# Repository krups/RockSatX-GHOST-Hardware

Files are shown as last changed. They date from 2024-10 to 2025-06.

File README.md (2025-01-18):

# RockSatX-GHOST-Hardware
PCB design files and documentation for the hardware used in the University of Kentucky's 2025 RockSat-XG KRUPS payload. Further information for each component is found in its respective folder.

### Hardware Folders
- [Capsule](Capsule)
- [FemtoSat](FemtoSat)
- [BaseStation/RocketStation](RocketStation)
- [LR62XE Adapter/Breakout](LR62XEAdapter)

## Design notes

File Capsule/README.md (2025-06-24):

# Capsule
PCB design files and documentation for the re-entry capsule used in the University of Kentucky's 2025 RockSat-XG KRUPS payload

### PCB Render
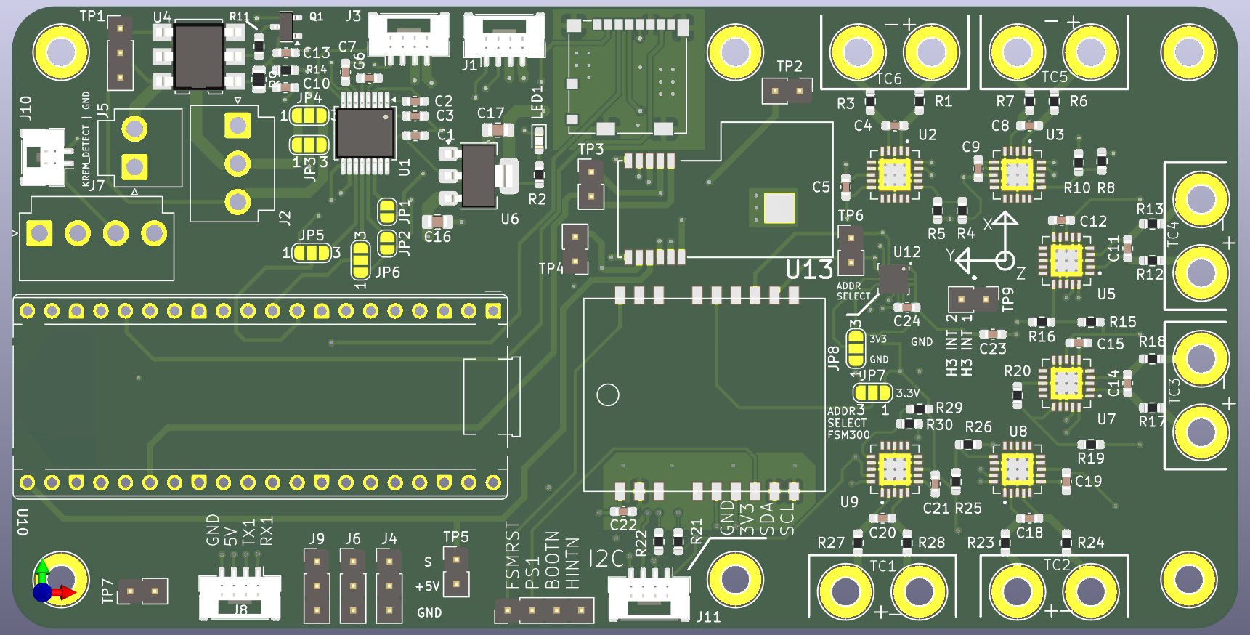
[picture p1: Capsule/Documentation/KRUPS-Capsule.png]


### Components
- [Raspberry Pi Pico 2 W (4MB Flash)](https://datasheets.raspberrypi.com/picow/pico-2-w-datasheet.pdf)
- [Fanstel LR62XE 1W 868/915MHz LoRa Modem](https://static1.squarespace.com/static/561459a2e4b0b39f5cefa12e/t/63ddc4b1dd728b424f1a6c23/1675478197953/LR62E_LR62XE_M262X840XE_Product+Specifications.pdf)
- [FSM300 9-Axis IMU](https://www.mouser.com/datasheet/2/1480/FSM30x_Datasheet-3196253.pdf)
- [H3LIS100DL 3-axis accelerometer](https://www.st.com/resource/en/datasheet/h3lis100dl.pdf)
- [MCP9600 thermocouple to digital converter](https://ww1.microchip.com/downloads/aemDocuments/documents/MSLD/ProductDocuments/DataSheets/MCP960X-L0X-RL0X-Thermocouple-EMF-to-Temperature-Converter-plus-minus-1-5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)

### Pin Mapping
| Pico 2 GPIO Pin | Net Name |
| --- | --- |
| GPIO0 | T_IRIDIUM |
| GPIO1 | R_IRIDIUM |
| GPIO2 | SDA |
| GPIO3 | SCL |
| GPIO4 | TX1 |
| GPIO5 | RX1 |
| GPIO6 | TX_GPS |
| GPIO7 | RX_GPS |
| GPIO12 | SD_SPI_MISO |
| GPIO13 | SD_SPI_CS |
| GPIO14 | SD_SPI_CLK |
| GPIO15 | SD_SPI_MOSI |
| GPIO16 | LORA_SPI_MISO |
| GPIO17 | LORA_SPI_CSN |
| GPIO18 | LORA_SPI_CLK |
| GPIO19 | LORA_SPI_MOSI |
| GPIO20 | LORA_ANTW |
| GPIO21 | LORA_RESET |
| GPIO22 | LORA_BUSY |
| GPIO26 | LORA_DIO1 |
| GPIO27 | PWMLS |

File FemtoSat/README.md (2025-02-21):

# KRUPS-FemtoSat
PCB design files and documentation for the femto-satellites used in the University of Kentucky's 2025 RockSat-XG KRUPS payload

### PCB Render
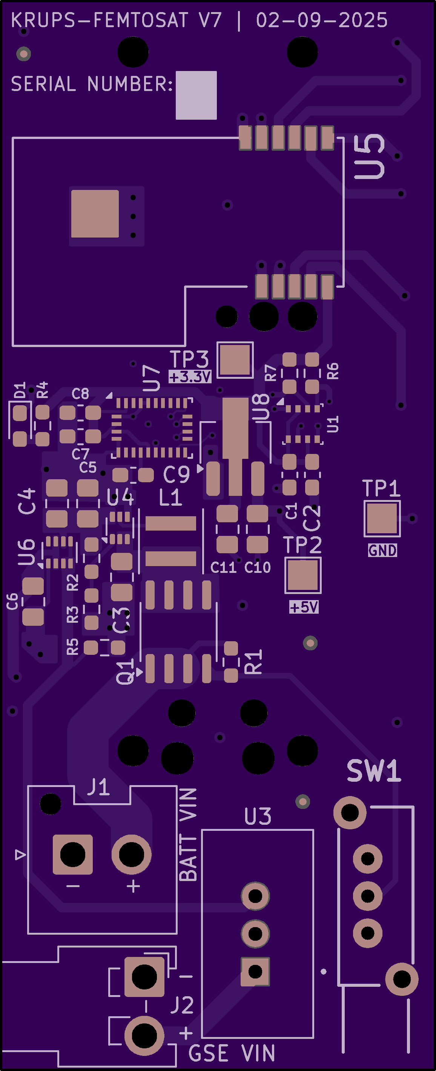
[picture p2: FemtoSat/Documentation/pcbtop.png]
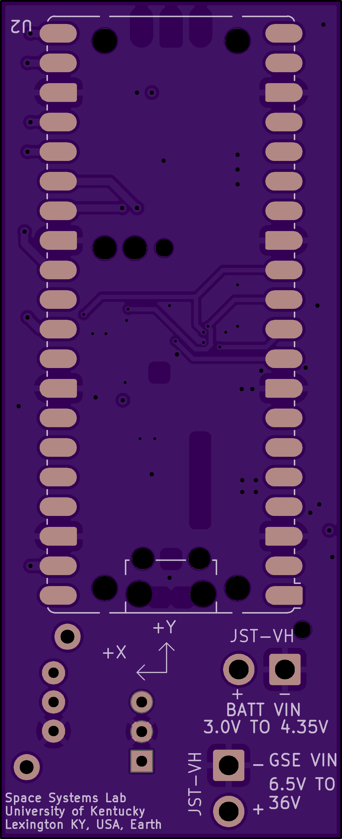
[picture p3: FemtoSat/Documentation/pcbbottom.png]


### Components
- [Raspberry Pi Pico 2 W (4MB Flash)](https://datasheets.raspberrypi.com/picow/pico-2-w-datasheet.pdf)
- [Fanstel LR62XE 1W 868/915MHz LoRa Modem](https://static1.squarespace.com/static/561459a2e4b0b39f5cefa12e/t/63ddc4b1dd728b424f1a6c23/1675478197953/LR62E_LR62XE_M262X840XE_Product+Specifications.pdf)
- [BME280 Temperature, Pressure, Humidity Sensor](https://www.bosch-sensortec.com/media/boschsensortec/downloads/datasheets/bst-bme280-ds002.pdf)
- [BNO086 9-Axis IMU](https://www.mouser.com/datasheet/2/1480/BNO080_085_Datasheet-3196201.pdf)

### Pin Mapping
| Pico 2 W GPIO Pin | Net Name |
| --- | --- |
| GPIO6 | BNO086_HINTN |
| GPIO7 | BNO086_RESET (active low)|
| GPIO8 | I2C_SDA |
| GPIO9 | I2C_SCL |
| GPIO16 | SPI_MISO |
| GPIO17 | SPI_NSS |
| GPIO18 | SPI_CLK |
| GPIO19 | SPI_MOSI |
| GPIO20 | LORA_ANTSW |
| GPIO21 | LORA_RESET (active low)|
| GPIO22 | LORA_BUSY |
| GPIO26 | LORA_DIO1 |

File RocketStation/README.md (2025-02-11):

# KRUPS-RocketStation
PCB design files and documentation for the base station/rocket station used in the University of Kentucky's 2025 RockSat-XG KRUPS payload

### PCB Render
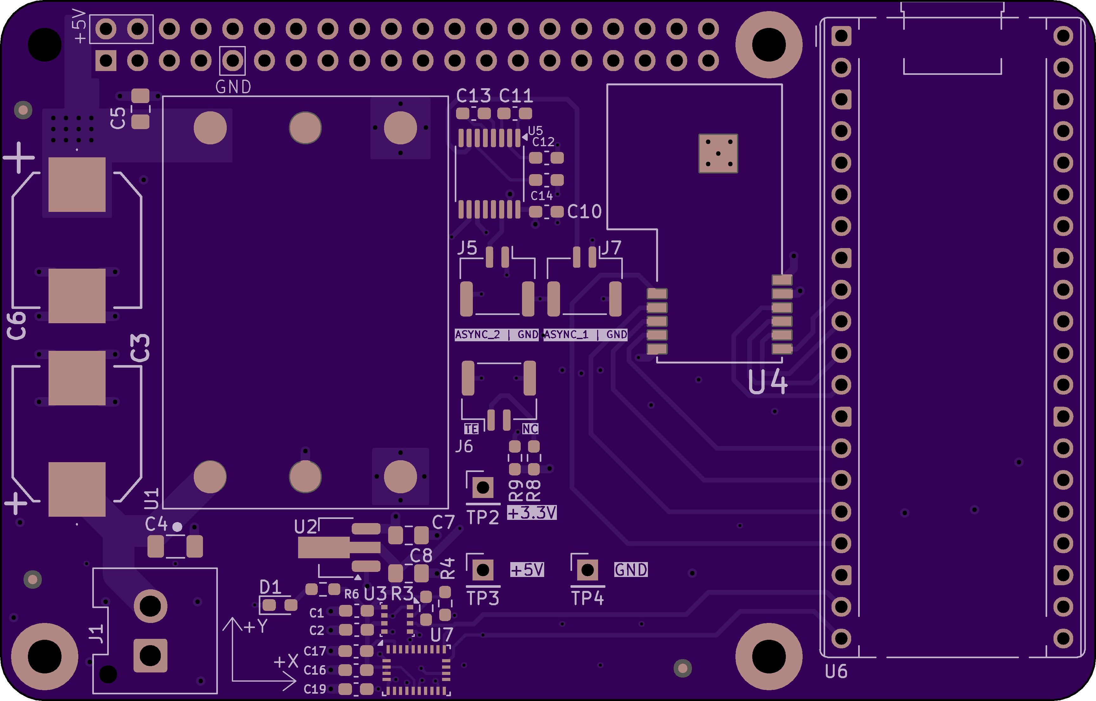
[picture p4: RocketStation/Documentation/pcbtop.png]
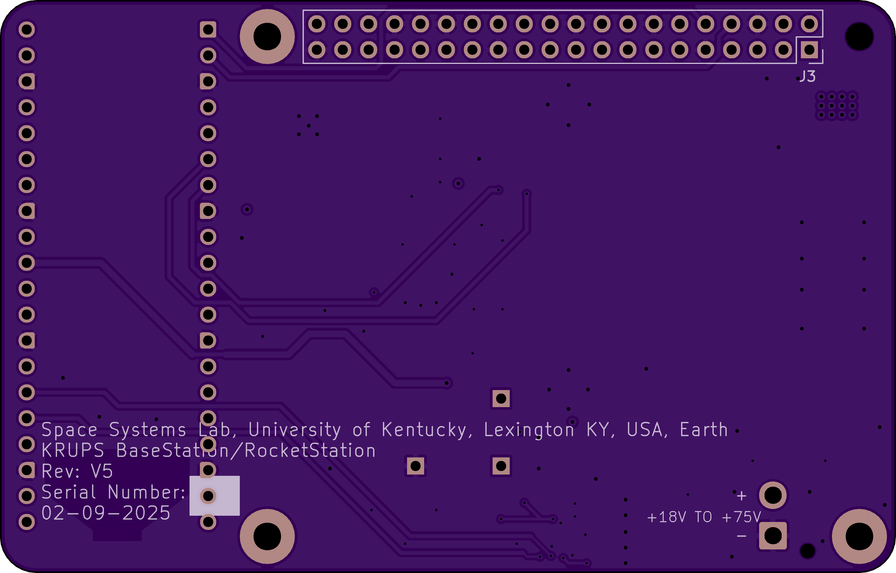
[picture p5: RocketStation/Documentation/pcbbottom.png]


### Components
- [Raspberry Pi Pico 2 W (4MB Flash)](https://datasheets.raspberrypi.com/picow/pico-2-w-datasheet.pdf)
- [Fanstel LR62XE 1W 868/915MHz LoRa Modem](https://static1.squarespace.com/static/561459a2e4b0b39f5cefa12e/t/63ddc4b1dd728b424f1a6c23/1675478197953/LR62E_LR62XE_M262X840XE_Product+Specifications.pdf)
- [BME280 Temperature, Pressure, Humidity Sensor](https://www.bosch-sensortec.com/media/boschsensortec/downloads/datasheets/bst-bme280-ds002.pdf)
- [BNO086 9-Axis IMU](https://www.mouser.com/datasheet/2/1480/BNO080_085_Datasheet-3196201.pdf)
- [PKU5511ESI DC/DC Step-down Converter](https://flexpowermodules.com/resources/fpm-techspec-pku5500e)

### Pin Mapping
| Pico 2 W GPIO Pin | Net Name |
| --- | --- |
| GPIO0 | RPI_UART4_TX |
| GPIO1 | RPI_UART4_RX |
| GPIO4 | ASYNC_UART_TX1 |
| GPIO5 | ASYNC_UART_TX2 |
| GPIO6 | SPI_CLK |
| GPIO7 | SPI_MOSI |
| GPIO8 | SPI_MISO |
| GPIO9 | SPI_NSS |
| GPIO10 | LORA_DIO1 |
| GPIO11 | LORA_BUSY |
| GPIO12 | LORA_RESET (active low)|
| GPIO13 | LORA_ANTSW |
| GPIO14 | I2C_SDA |
| GPIO15 | I2C_SCL |
| GPIO19 | BNO086_RESET (active low) |
| GPIO20 | BNO086_HINTN |
| GPIO26 | TE_SENSE (ADC) |

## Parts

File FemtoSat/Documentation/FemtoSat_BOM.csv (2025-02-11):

Reference | Value | Description | Qty | Digikey Part Number | DNP
C1,C2,C7,C8,C9 | 0.1u | 0.1uF, 16V, X7R, SMD 0603 | 5 | CC0603KRX7R7BB104
C3,C6,C10 | 10u | 10uF, 16V, X5R, SMD 0805 | 3 | CL21A106KOQNNNG
C4,C5,C11 | 22u | 22uF, 10V, X5R, SMD 0805 | 3 | CL21A226MPQNNNE
D1 | LED | LED, 1.95V Vf, 20mA If, SMD 0603 | 1 | APT1608SURCK
J1 | B2P-VH-FB-B | JST-VH 2 Pin Connector, Shielded, Vertical | 1 | B2P-VH-FB-B
J2 | B2PS-VH | JST-VH 2 Pin Connector, Horizontal | 1 | B2PS-VH
L1 | 1u | 1uH Inductor, Shielded | 1 | XEL4030-102MEC
Q1 | IRF7410 | PMOSFET, SOIC-8 | 1 | IRF7410TRPBF
R1,R5 | 100k | 100K OHM, 1%, 1/10W, SMD 0603 | 2 | RMCF0603FT100K
R2 | 73.2k | 73.2K OHM, 1%, 1/10W, SMD 0603 | 1 | RC0603FR-0773K2L
R3 | 10k | 10K OHM, 1%, 1/10W, SMD 0603 | 1 | RC0603FR-0710KL
R4 | 68 | 68 OHM, 5%, 1/10W, SMD 0603 | 1 | RC0603JR-0768RL
R6,R7 | 3.9k | 3.9K OHM, 1%, 1/10W, SMD 0603 | 2 | ERJ-3EKF3901V
SW1 | Enclosure Detector | SPDT Push Switch, Non-Latching | 1 | LC1258OANP
U1 | BME280 | 3-in-1 sensor, humidity, pressure, temperature, I2C and SPI interface, 1.71-3.6V, LGA-8 | 1 | BME280
U2 | Pico_2_W | Versatile and inexpensive microcontroller module powered by an RP2350 dual-core processor | 1 | 2648-SC1633CT-ND
U3 | TSR_2-2450 | 1A step-down regulator module, fixed 5V output voltage, 5-36V input voltage, -40°C to +85°C temperature range, TO-220 compatible LM78xx replacement | 1 | TSR 2-2450
U4 | TPS61023 | TPS61023 Boost Converter | 1 | TPS61023DRLR
U5 | LR62XE | 1W LoRa Module | 1 | LR62XE
U6 | TPS2117 | 2 Channnels Power Mux with Manual and Priority Switchover, 1.6-5.5V Input Voltage, 2.5A Output Current, Ron 40 mOhm, SOT-583-8 | 1 | TPS2117DRLR
U7 | BNO086 | Accelerometer, Gyroscope, Magnetometer, Temperature, 9 Axis Sensor IC, SPI Output | 1 | BNO086
U8 | AZ1117-3.3 | 1A 20V Fixed LDO Linear Regulator, 3.3V, SOT-89/SOT-223/TO-220/TO-252/TO-263 | 1 | AZ1117CR2-3.3TRG1

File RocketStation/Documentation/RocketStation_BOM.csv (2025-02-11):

Reference | Value | Description | Qty | DNP | Digikey Part Number
C1,C2,C10,C11,C12,C13,C14,C16,C17,C19 | 0.1u | 0.1uF, 16V, X7R, SMD 0603 | 10 |  | CC0603KRX7R7BB104
C3 | 100u | 100uF, 63V, Aluminum Electrolytic, SMD | 1 |  | A768MS107M1JLAV027
C4 | 2.2u | 2.2uF, 100V, X7R, SMD 1206 | 1 |  | 12061C225KAT2A
C5,C8 | 22u | 22uF, 10V, X5R, SMD 0805 | 2 |  | CL21A226MPQNNNE
C6 | 470u | 470uF, 25V, Aluminum Electrolytic, SMD | 1 |  | A768MS477M1ELAV017
C7 | 10u | 10uF, 16V, X5R, SMD 0805 | 1 |  | CL21A106KOQNNNG
D1 | LED | LED, 1.95V Vf, 20mA If, SMD 0603 | 1 |  | APT1608SURCK
J1 | B2P-VH-FB-B | JST-VH 2 Pin Connector, Shielded, Vertical | 1 |  | B2P-VH-FB-B
J3 | RPi5_Header | Expansion header for Raspberry Pi 5 | 1 |  | PRT-16764
J5,J6,J7 | BM02B-GHS-TBT | JST-GH 2 Pin Connector, Vertical | 3 |  | BM02B-GHS-TBT
R3,R4 | 3.9k | 3.9K OHM, 1%, 1/10W, SMD 0603 | 2 |  | ERJ-3EKF3901V
R6 | 68 | 68 OHM, 5%, 1/10W, SMD 0603 | 1 |  | RC0603JR-0768RL
R8 | 20k | 20K OHM, 1%, 1/10W, SMD 0603 | 1 |  | ERJ-3EKF2002V
R9 | 2k | 2K OHM, 1%, 1/10W, SMD 0603 | 1 |  | ERJ-3EKF2001V
U1 | PKU5511ESI | DC/DC Step Down, 1/16 brick | 1 |  | PKU5511ESI
U2 | AZ1117-3.3 | 1A 20V Fixed LDO Linear Regulator, 3.3V, SOT-89/SOT-223/TO-220/TO-252/TO-263 | 1 |  | AZ1117CR2-3.3TRG1
U3 | BME280 | 3-in-1 sensor, humidity, pressure, temperature, I2C and SPI interface, 1.71-3.6V, LGA-8 | 1 |  | BME280
U4 | LR62XE |  | 1
U5 | SP3232 | SP3232 RS-232 Level Shifter, TSSOP-16 | 1 |  | SP3232EUEY-L/TR
U6 | Pico_2_W | Versatile and inexpensive microcontroller module powered by an RP2350 dual-core processor | 1
U7 | BNO086 | Accelerometer, Gyroscope, Magnetometer, Temperature, 9 Axis Sensor IC, SPI Output | 1 |  | BNO086

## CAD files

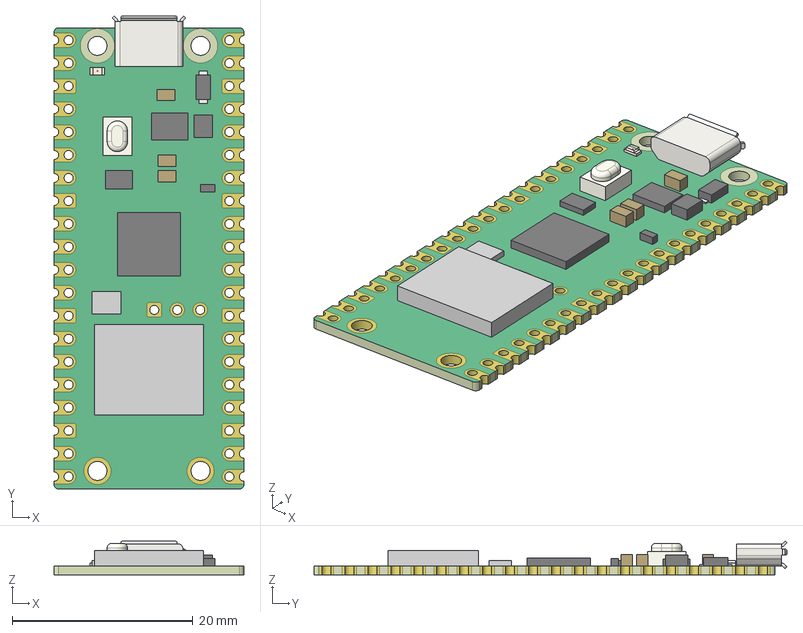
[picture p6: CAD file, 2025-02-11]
FemtoSat/KiCadProjectFiles/Imported/STEP/RaspberryPi_Pico_W.step
21.0 x 52.3 x 3.75 mm
Pico_W_Board
C1_47u
C2_47u
C21_47u
D1_MBR120VLSFT1G
D2_QSME-C194_Base
D2_QSME-C194_Phosphor
D2_QSME-C194_Lens
J1_690T505-x62-01x
L1_2u2
Q1_DMG1012T
SH1_CYW43439
SW1_TP-1221U-K9K5325
U1_RP2040
U2_RT6154AGQW
U3_W25Q16JVUXIQ
X1_X12M000000S096

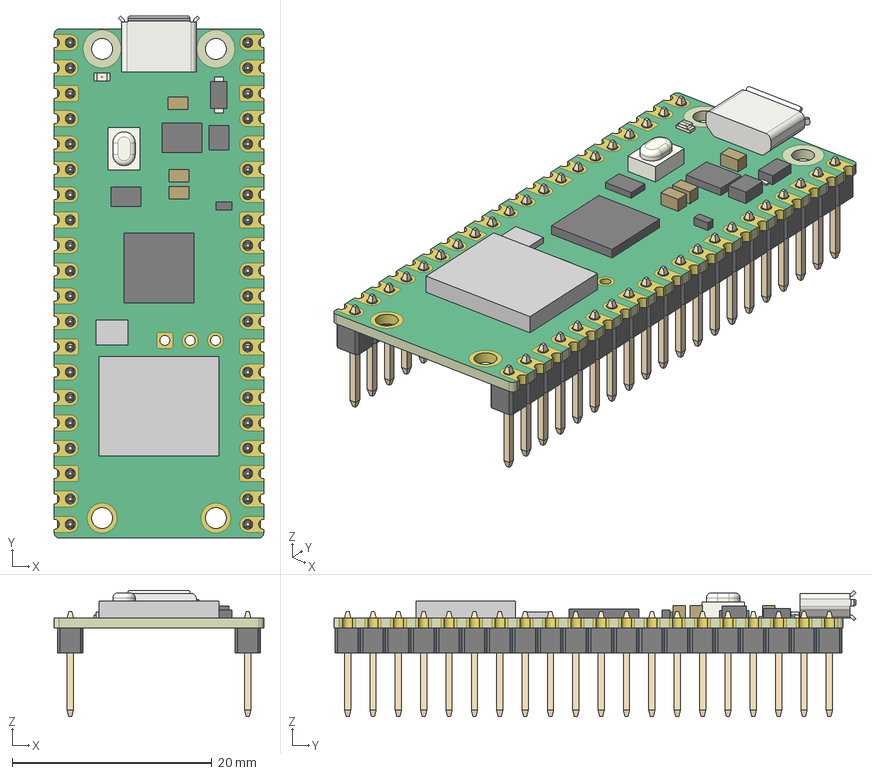
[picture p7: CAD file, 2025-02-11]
RocketStation/KiCadProjectFiles/Imported/STEP/RaspberryPi_Pico_W_AddedHeaders.step
21.0 x 52.3 x 12.6 mm
Pico_W_Board
C1_47u
C2_47u
C21_47u
D1_MBR120VLSFT1G
D2_QSME-C194_Base
D2_QSME-C194_Phosphor
D2_QSME-C194_Lens
J1_690T505-x62-01x
L1_2u2
Q1_DMG1012T
SH1_CYW43439
SW1_TP-1221U-K9K5325
U1_RP2040
U2_RT6154AGQW
U3_W25Q16JVUXIQ
X1_X12M000000S096
Header_Breakaway x 2

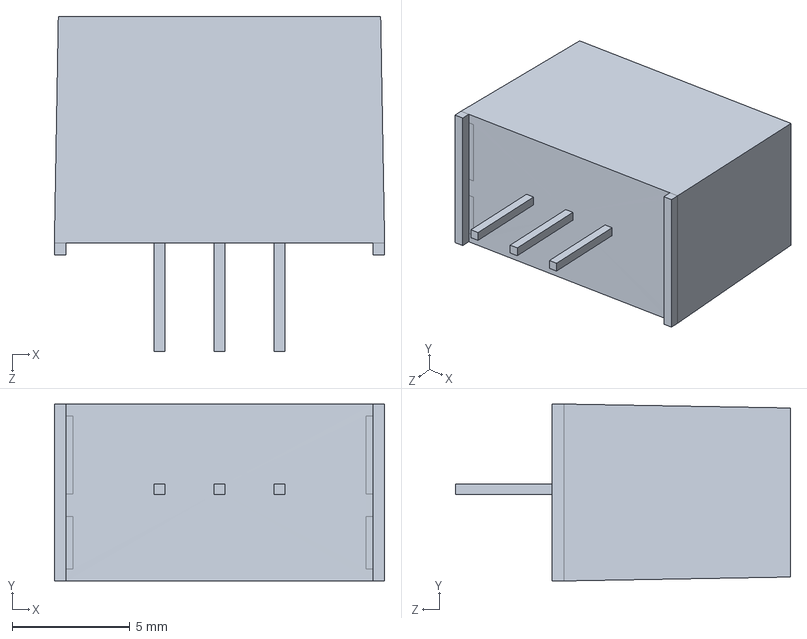
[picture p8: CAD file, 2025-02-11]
FemtoSat/KiCadProjectFiles/Imported/STEP/TSR2-2450.stp
14.0 x 7.50 x 14.2 mm

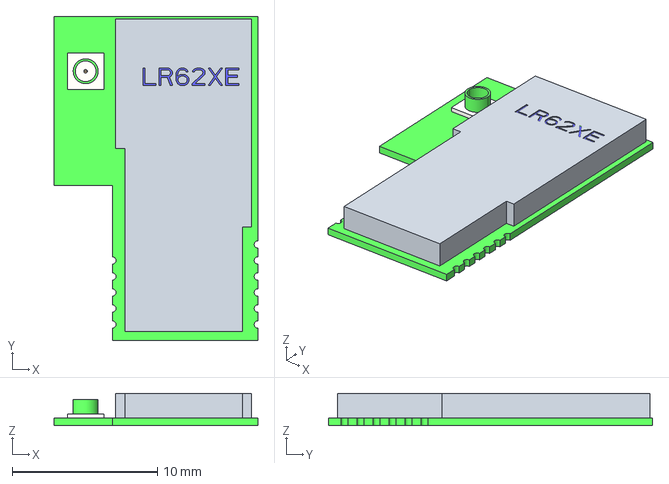
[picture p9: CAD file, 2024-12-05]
RocketStation/KiCadProjectFiles/Imported/STEP/lr62xe.stp
14.0 x 22.3 x 2.20 mm

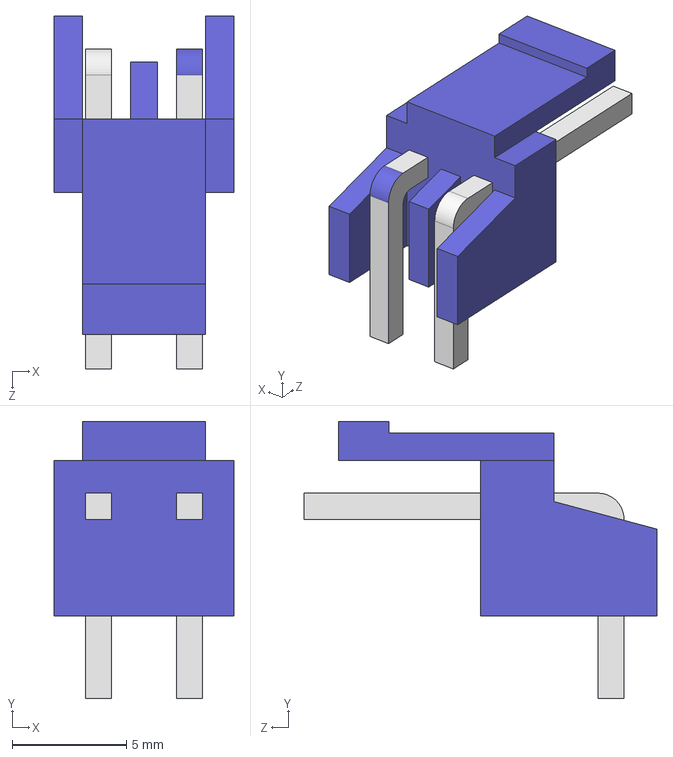
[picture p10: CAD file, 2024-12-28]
FemtoSat/KiCadProjectFiles/Imported/STEP/S2P-VH.STEP
7.86 x 12.1 x 15.4 mm

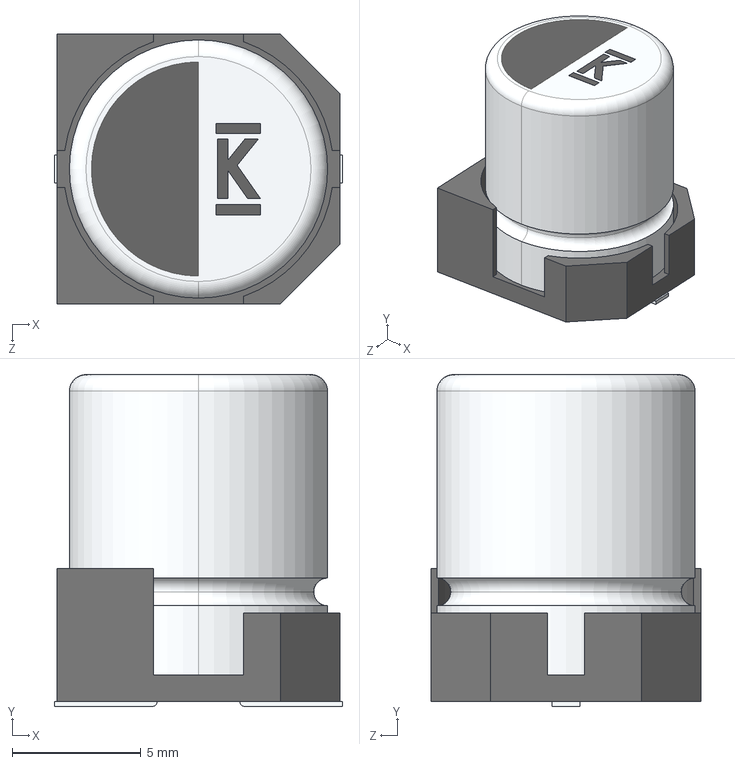
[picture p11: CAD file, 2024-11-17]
RocketStation/KiCadProjectFiles/Imported/STEP/A768MS.step
11.2 x 12.9 x 10.5 mm

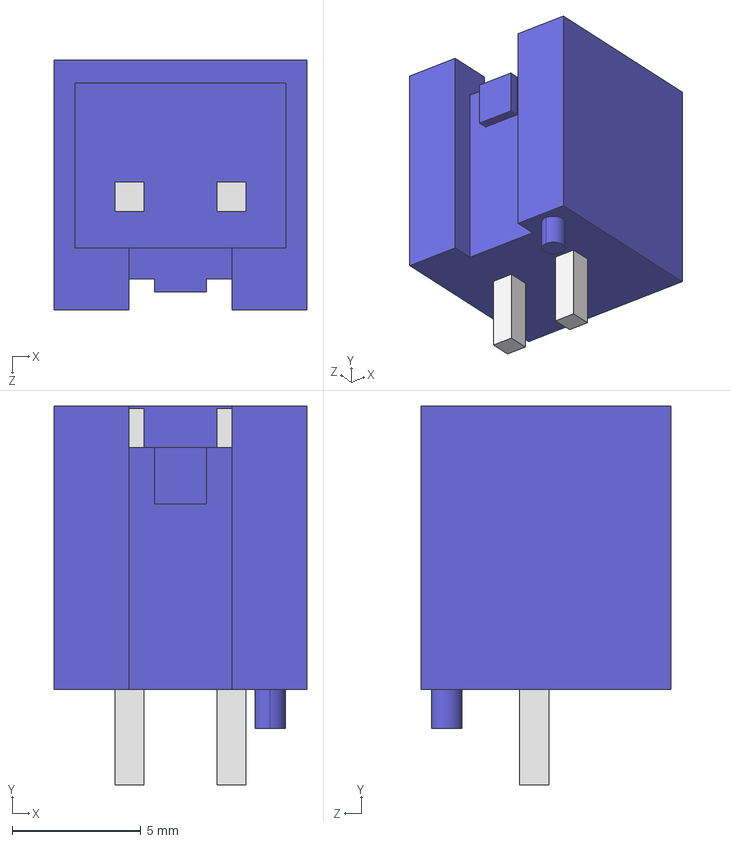
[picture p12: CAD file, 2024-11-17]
FemtoSat/KiCadProjectFiles/Imported/STEP/B2P-VH-FB-B.STEP
9.80 x 14.7 x 9.70 mm

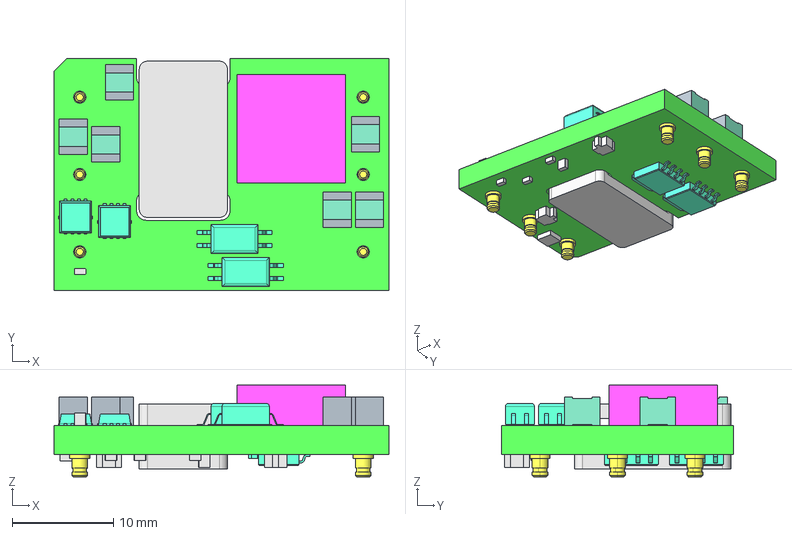
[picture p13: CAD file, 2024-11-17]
RocketStation/KiCadProjectFiles/Imported/STEP/PKU5511ESI.stp
33.0 x 22.9 x 9.04 mm
SNF901066 x 6
C2 x 6
M1 x 2
OP2 x 2
Ferrite-core x 2
chock
C26 x 3
T210 x 2
R15 x 2
Mosfet1 x 2
X.RYN1214604.2F.2
BOARD_PART

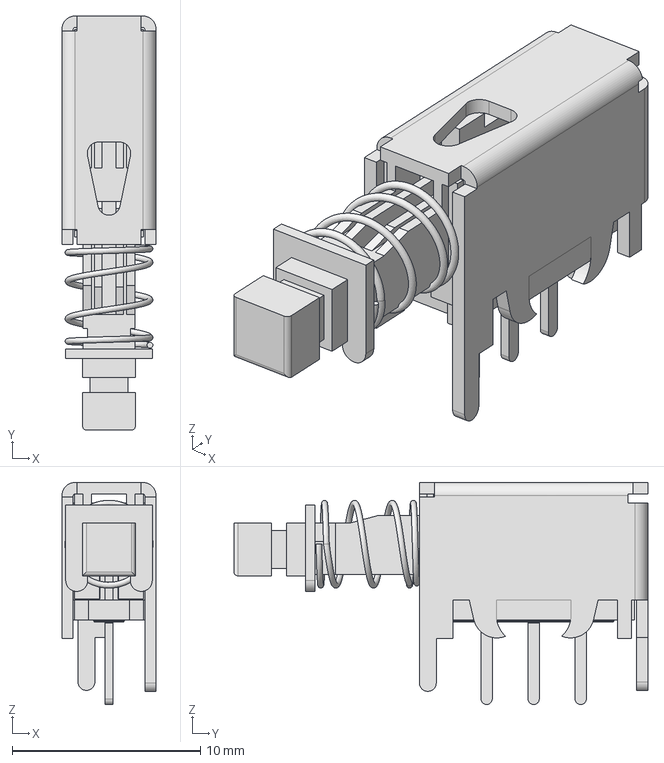
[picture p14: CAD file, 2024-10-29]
FemtoSat/KiCadProjectFiles/Imported/STEP/LC1258OANP.stp
5.00 x 22.0 x 11.8 mm

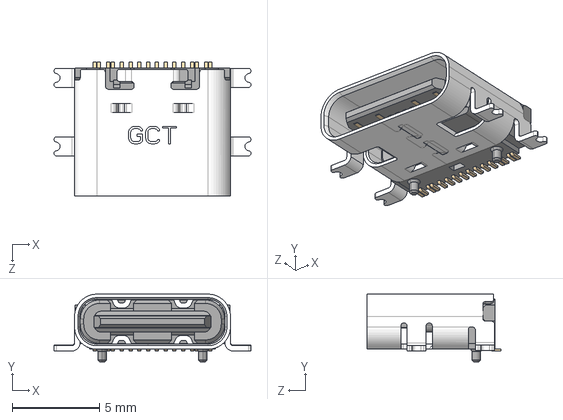
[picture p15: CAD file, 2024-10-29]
RocketStation/KiCadProjectFiles/Imported/STEP/USB4110GFA.step
11.3 x 3.89 x 7.70 mm

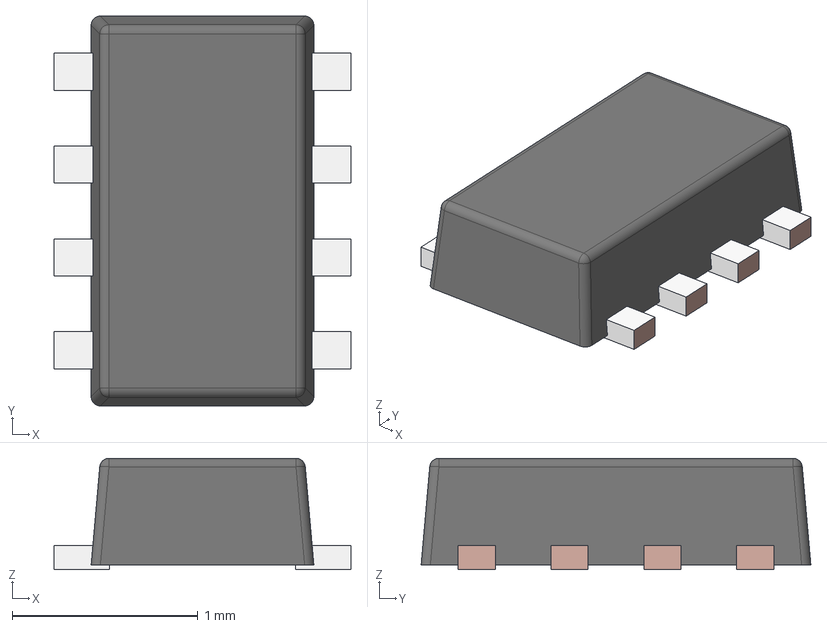
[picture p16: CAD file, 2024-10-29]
FemtoSat/KiCadProjectFiles/Imported/STEP/SOT-583.stp
1.60 x 2.10 x 0.6 mm
FRAME-DRL0008A
BODY-SOT

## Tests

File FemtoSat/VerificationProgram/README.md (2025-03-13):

## Femtosat Verification Program

Simple program that uses a pico debugger to verify that the BME280, BNO086, and LR62XE on a newly assembled femtosat are working. 

## Usage
Import this folder as a project into the VS Code Raspberry Pi Pico extension:
1. Set up your Raspberry Pi Pico development environment by following chapter 3 of [this](https://datasheets.raspberrypi.com/pico/getting-started-with-pico.pdf) guide
2. Clone this repo and its submodules using your preferred method.
- If you're new to git, I'd recommend [Github Desktop](https://github.com/apps/desktop).
- If you're downloading a zip archive from Github, make sure that you download each linked submodule (external repositories linked in the lib folder) manually as they will not be included.
2. Click "Import Project" under the General tab from within the extension.
3. Select the location of this folder
4. Change the debugger from DebugProbe to SWD (If you're using a pico to debug. If you're using the debug probe, leave it as-is.)
5. Click "Import"
6. Click "Configure CMake" under the Project tab from within the extension.
7. Set a debugging breakpoint in main.cpp in the src folder. It should be near line 121, with a comment saying BREAKPOINT HERE
8. Power on the femtosat with a bench top power supply. 9V to the GSE input usually works fine. Pay attention to polarity.
9. Connect the debugger wires to the debugging header on the pico. 
- Starting from the board edge going to the center, the wire colors should be orange, black, yellow (with the pico debug probe).
10. Debug the project from the pico extension window. This will start a debugging session.
11. Continue the debugging session until you hit the breakpoint set earlier
12. Verify that the initialization state variables in the debugger match the expected values. 
- If not, that sensor is not operational. Check solder joints and replace the component if necessary.
- Error code specifics can be found [here](https://jgromes.github.io/RadioLib/group__status__codes.html) for the LoRa module, and within lib\BME280_Drivers\bme280_defs.h for the BME280. The BNO086 does not give any useful error codes.

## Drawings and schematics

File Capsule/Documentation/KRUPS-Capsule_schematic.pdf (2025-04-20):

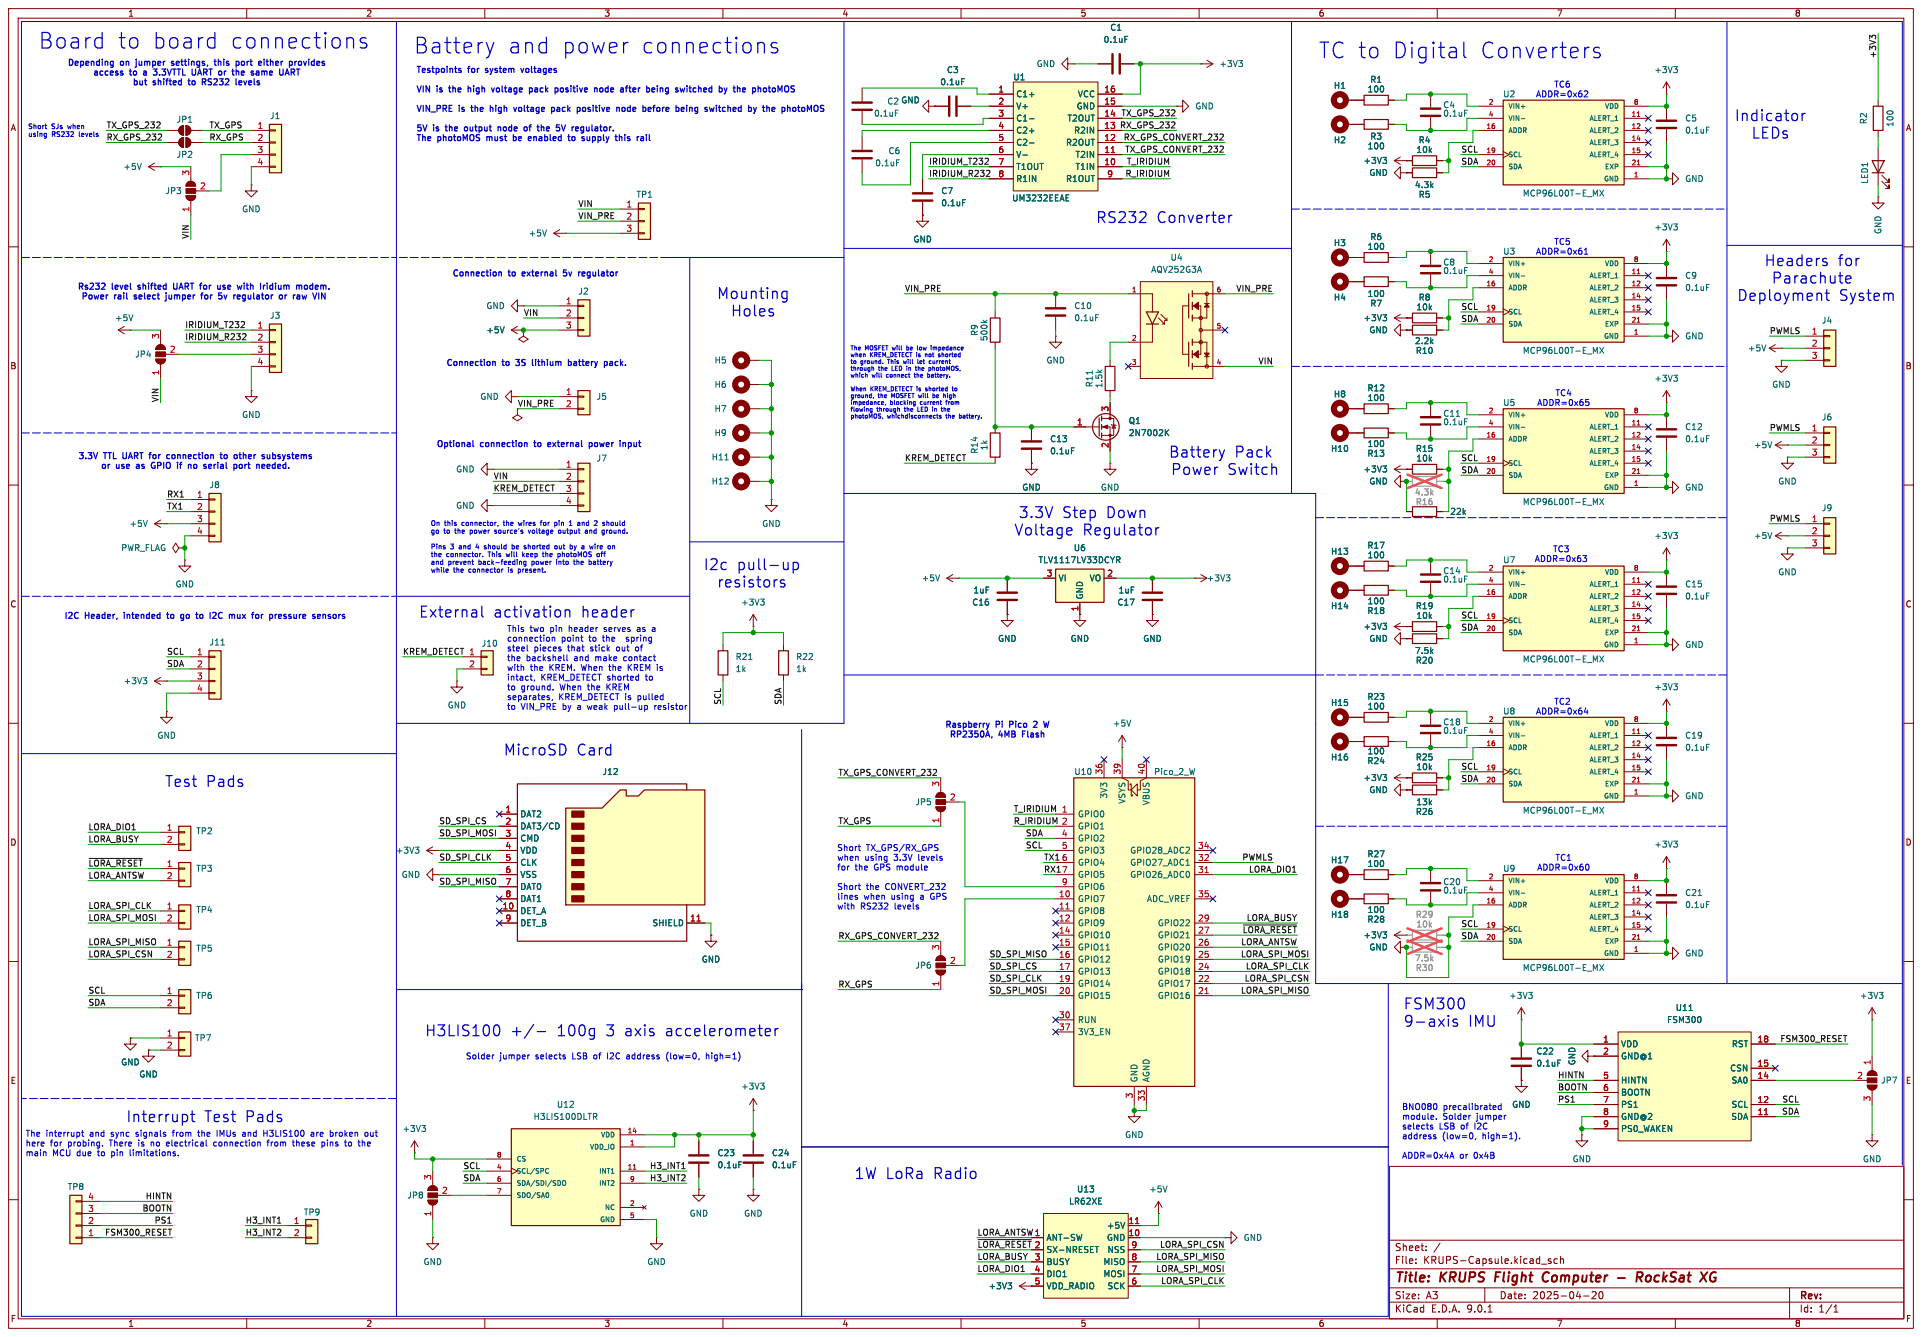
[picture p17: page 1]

T_IRIDIUM Board to board connections

TC to Digital Converters

Depending on jumper settings, this port either provides
access to a 3.3VTTL UART or the same UART

VIN_PRE is the high voltage pack positive node before being switched by the photoMOS

Connection to external 5v regulator
H6 GND

3.3V TTL UART for connection to other subsystems or use as GPIO if no serial port needed. Rs232 level shifted UART for use with Iridium modem. Power rail select jumper for 5v regulator or raw VIN

The MOSFET will be low impedance when KREM_DETECT is not shorted

Connection to 3S lithium battery pack.

Optional connection to external power input
0.1uF GND GND

steel pieces that stick out of

to ground. When the KREM

RP2350A, 4MB Flash Short TX_GPS/RX_GPS when using 3.3V levels

TC1 ADDR=0x60 BNO080 precalibrated module. Solder jumper selects LSB of I2C

for the GPS module Short the CONVERT_232

lines when using a GPS with RS232 levels

Id: 1/1 Title: KRUPS Flight Computer - RockSat XG

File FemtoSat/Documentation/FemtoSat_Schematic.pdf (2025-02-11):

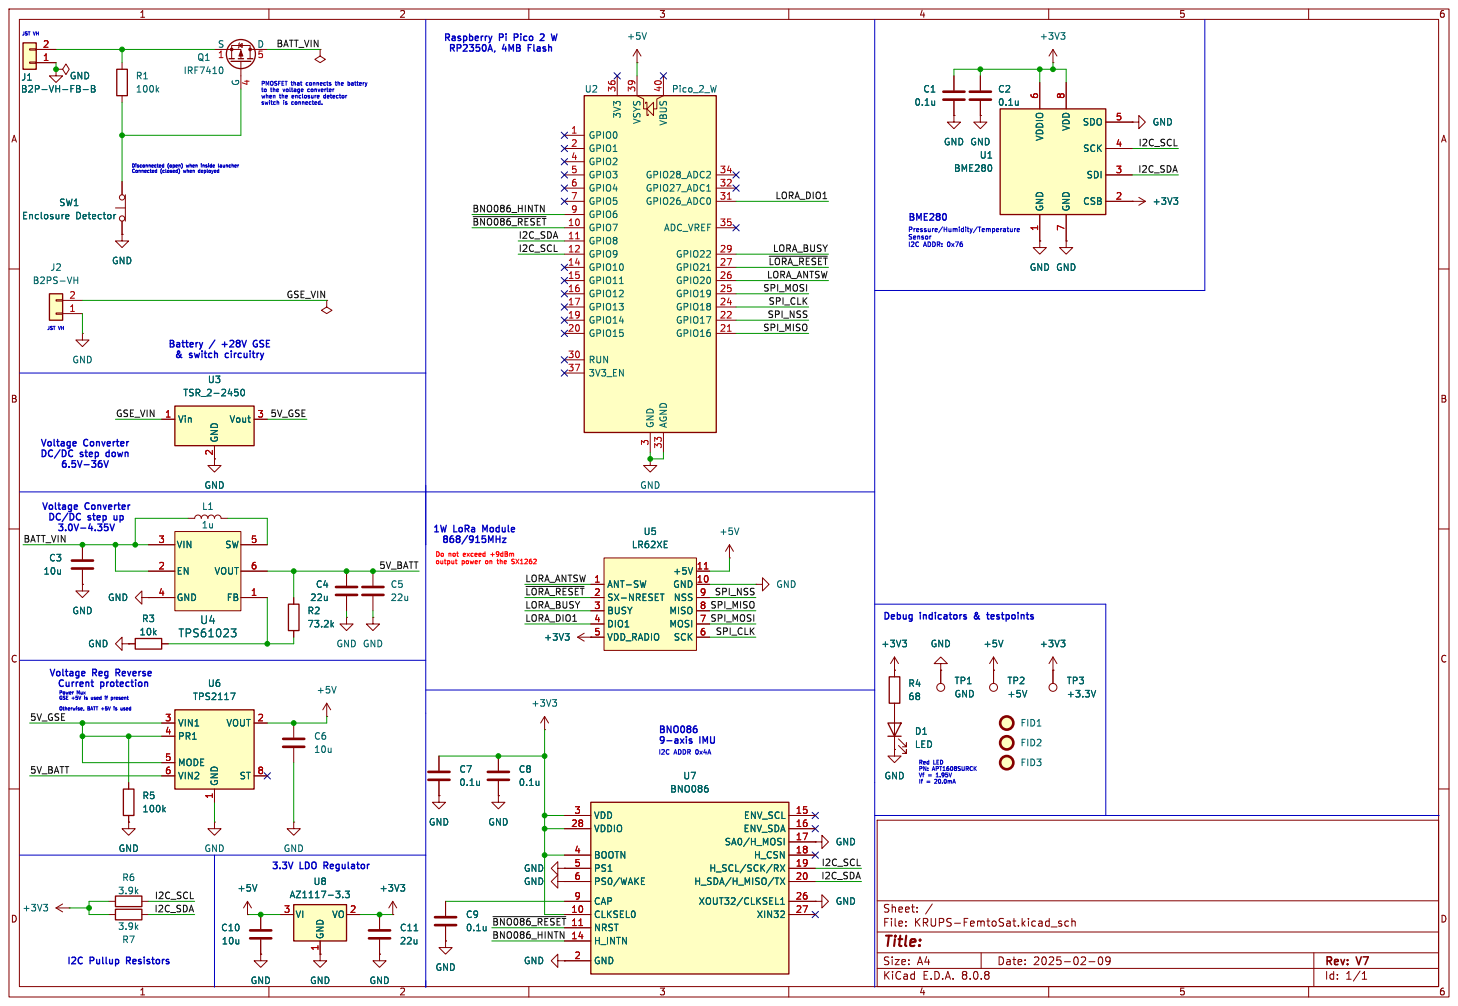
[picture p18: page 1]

1 CSB 2 SDI 3 SCK 4 SDO 5 VDDIO

BME280 Voltage Converter DC/DC step up

868/915MHz Voltage Converter DC/DC step down

1 VOUT 2 VIN1 3 PR1 4 MODE 5 VIN2 6 ST 8 GND GND

1 VOUT 2 VIN1 3 PR1 4 MODE 5 VIN2 6 ST 8 U6 TPS2117 GND

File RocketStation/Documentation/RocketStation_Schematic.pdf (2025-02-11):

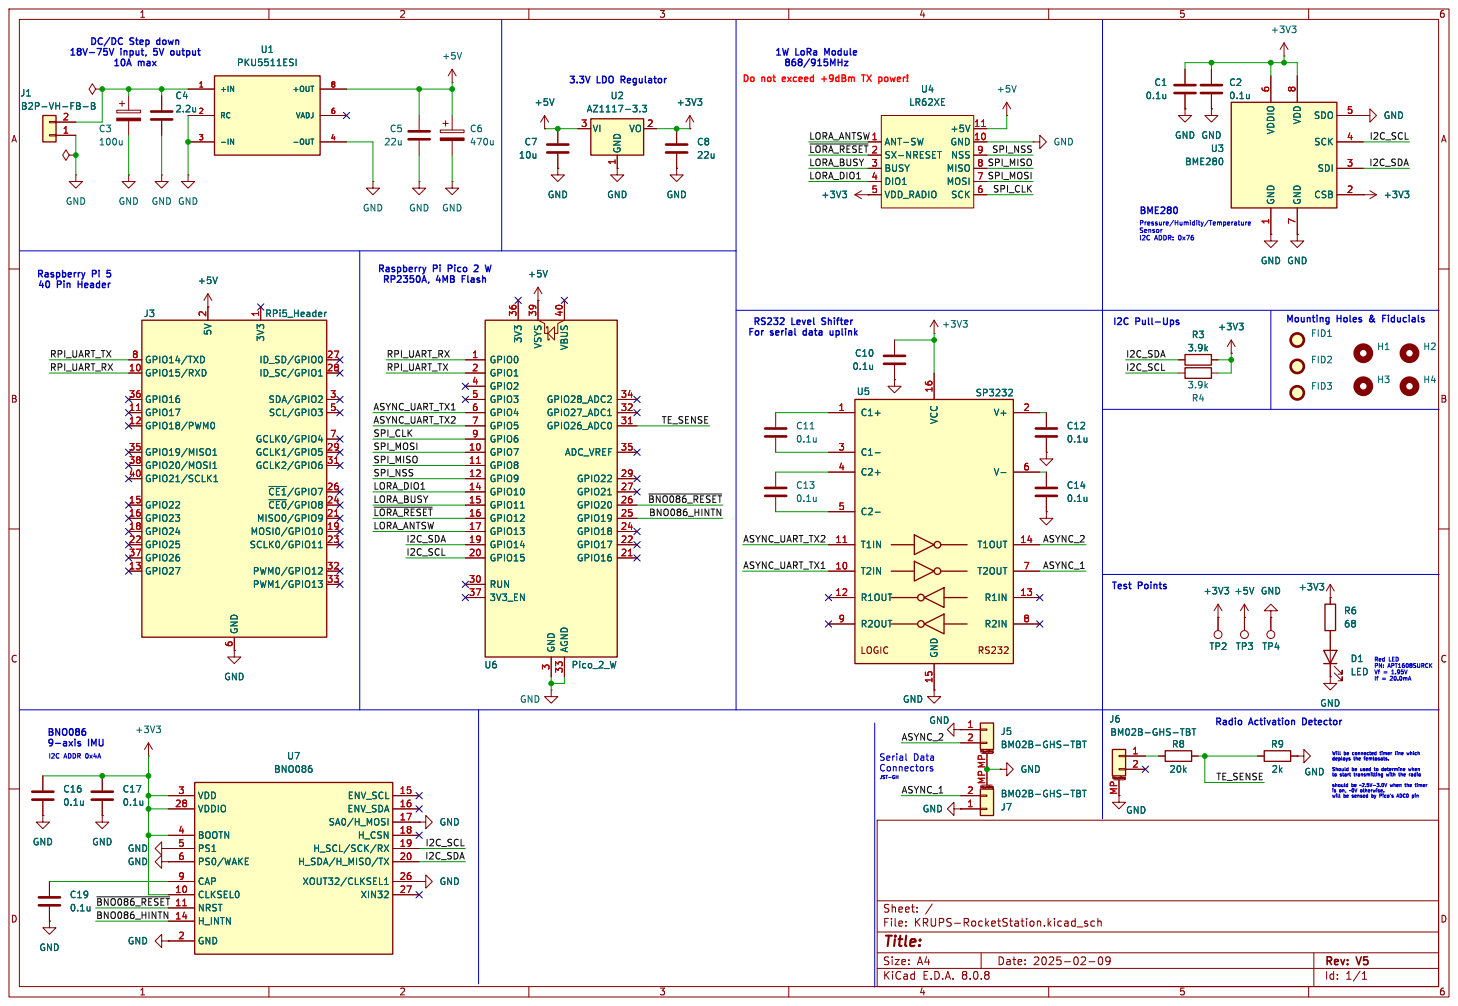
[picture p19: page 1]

DC/DC Step down

1 CSB 2 SDI 3 SCK 4 SDO 5 VDDIO

Pressure/Humidity/Temperature Sensor

If = 20.0mA Raspberry Pi Pico 2 W
RP2350A, 4MB Flash

6 GCLK0/GPIO4 7 GPIO14/TXD 8 +5V U7 BNO086 CLKSEL0 10 NRST 11 H_INTN 14 ENV_SCL 15 ENV_SDA 16 SA0/H_MOSI 17 H_CSN 18 H_SCL/SCK/RX 19 GND 2 H_SDA/H_MISO/TX 20 XOUT32/CLKSEL1 26 XIN32 27 VDDIO 28 VDD 3 BOOTN 4 PS1 5 PS0/WAKE 6 CAP 9 GND GND

J5BM02B-GHS-TBT GND GND

Id: 1/1 Title: File: KRUPS-RocketStation.kicad_sch Sheet: / GND

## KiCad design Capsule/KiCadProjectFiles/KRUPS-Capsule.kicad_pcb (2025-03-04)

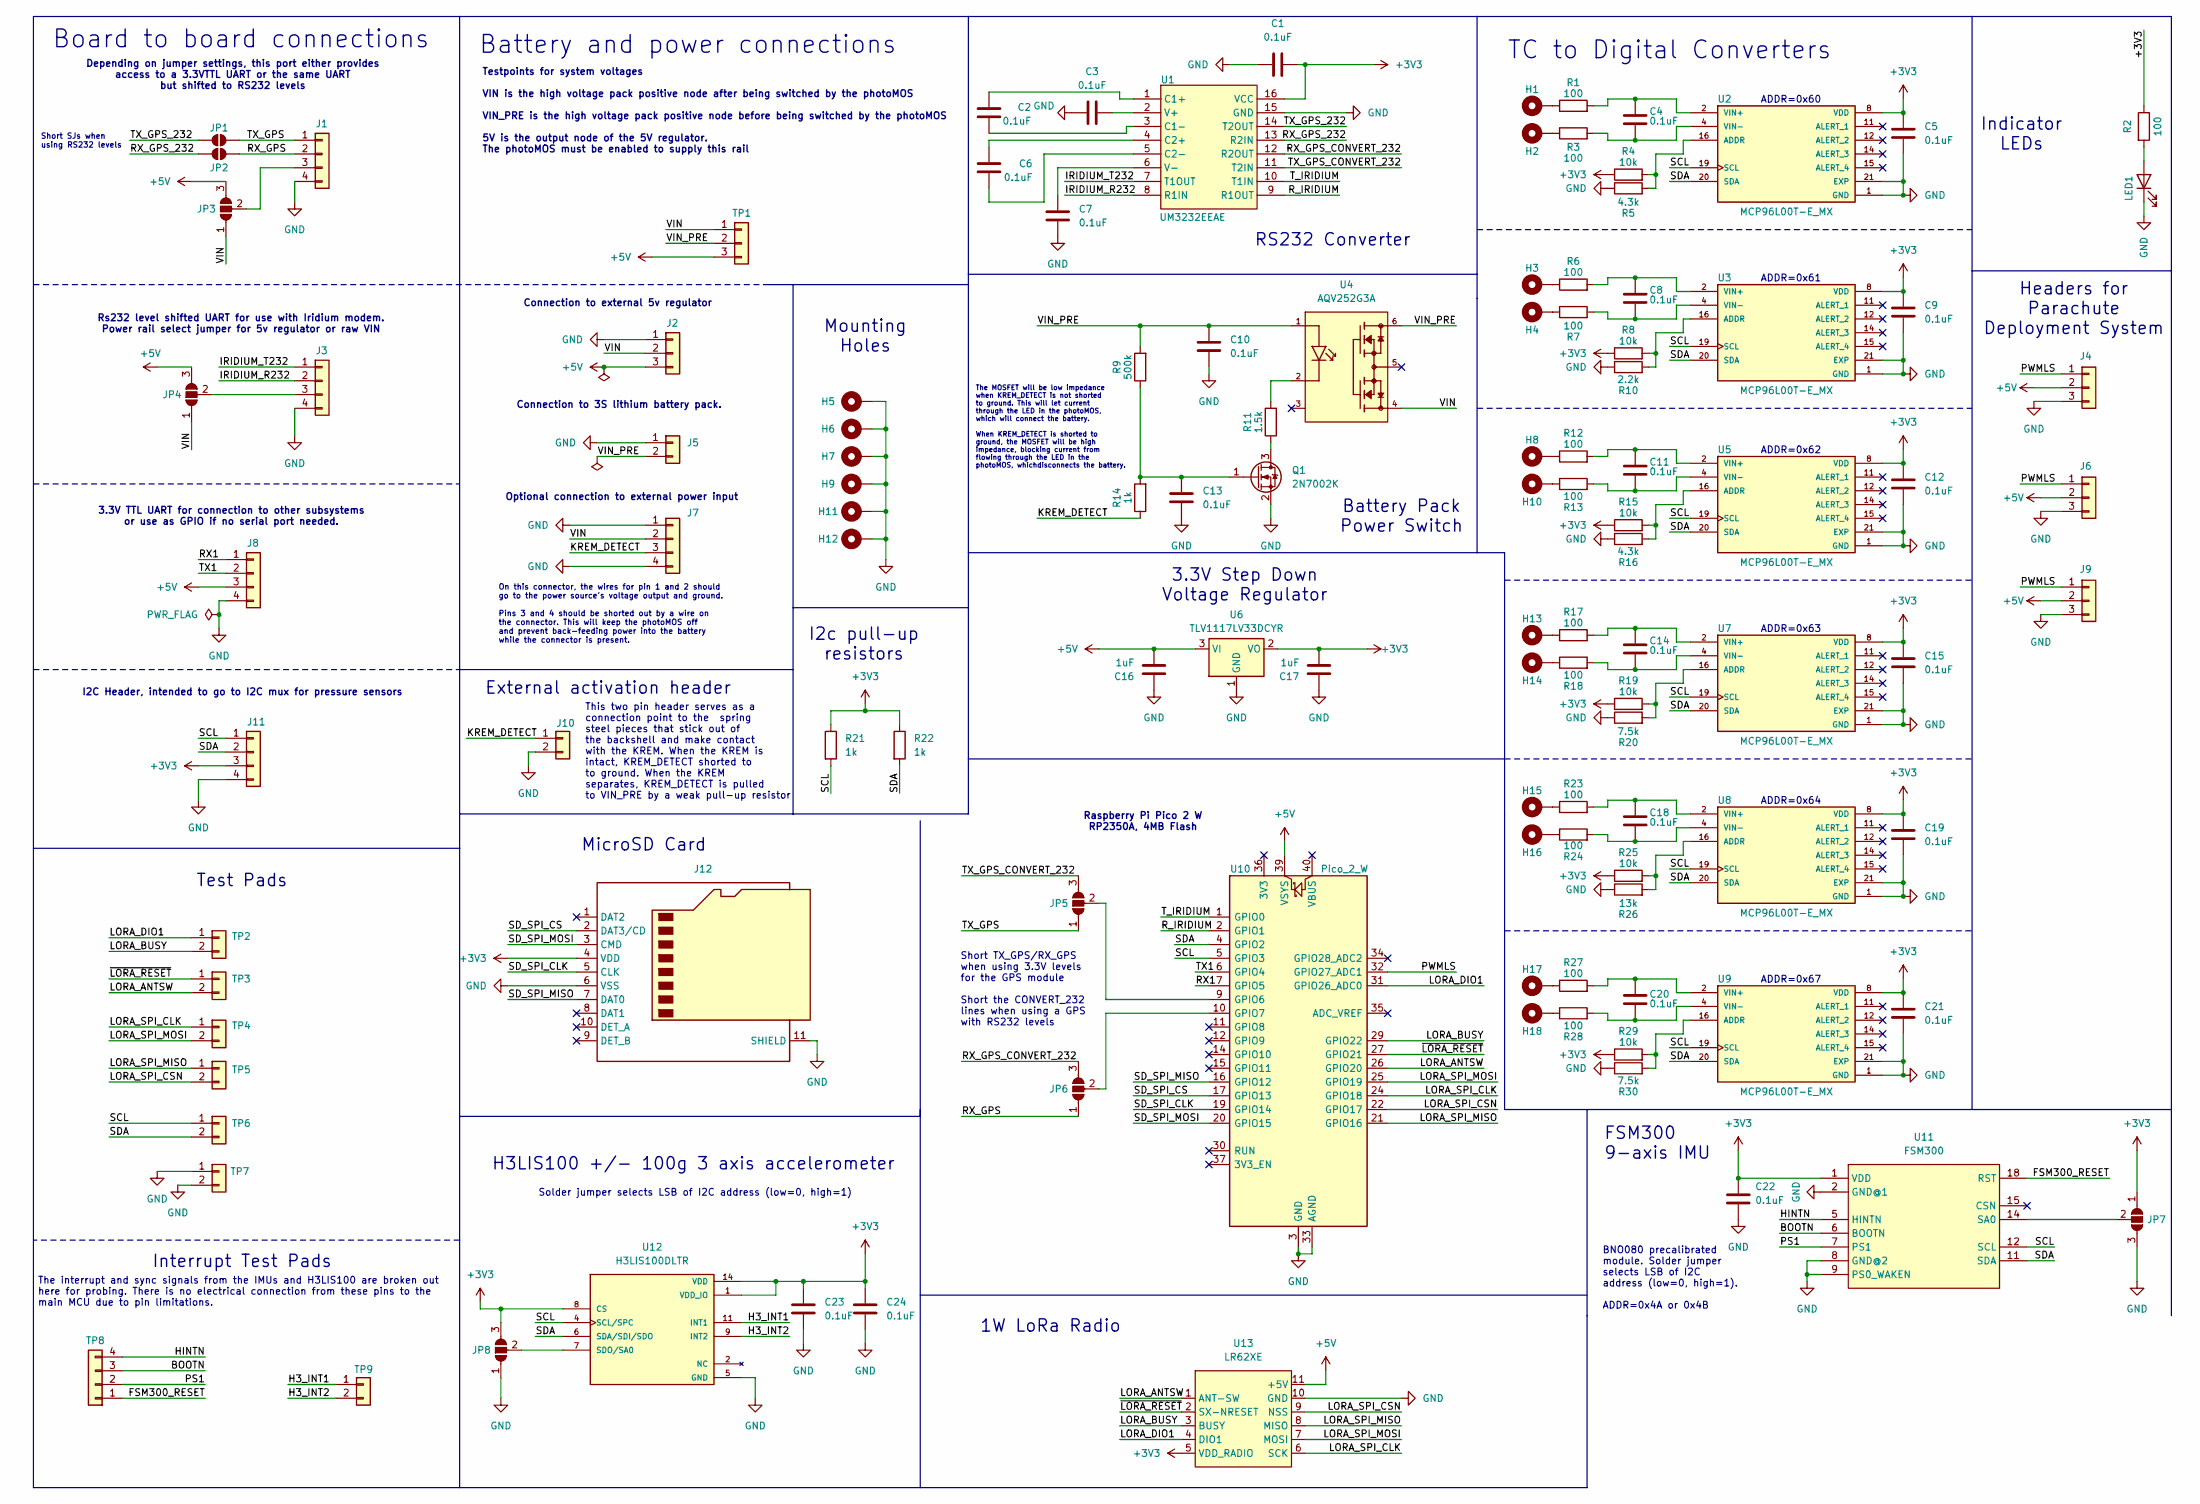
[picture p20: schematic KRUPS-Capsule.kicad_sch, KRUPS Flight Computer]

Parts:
C1, C2, C3, C4, C5, C6, C7, C8, C9, C10, C11, C12, C13, C14, C15, C18, C19, C20, C21, C22, C23, C24: 0.1uF; C_0603_1608Metric_Pad1.08x0.95mm_HandSolder; Digikey Part Number 0603B104K500XD
C16, C17: 1uF; C_0805_2012Metric_Pad1.18x1.45mm_HandSolder; Digikey Part Number 3372-0805B105K100CCTR-ND
H1, H2, H3, H4, H5, H6, H7, H8, H9, H10, H11, H12, H13, H14, H15, H16, H17, H18: MountingHole_Pad; 2,8-PAD
J1, J3: JST_GH_BM04B; JST_GH_BM04B-GHS-TBT_1x04-1MP_P1.25mm_Vertical; Digikey Part Number 455-BM04B-GHS-TBTTR-ND
J2: JST_VH_B4P-VH-B; JST_VH_B3P-VH-B_1x03_P3.96mm_Vertical; Digikey Part Number 455-B4P-VH-B-ND
J4, J6, J9: PinHeader_1x03_P2.54mm_Vertical; Digikey Part Number 732-5316-ND
J5: JST_VH_B2P; JST_VH_B2P-VH-B_1x02_P3.96mm_Vertical; Digikey Part Number 455-1639-ND
J7: Conn_01x04; JST_VH_B4P-VH-B_1x04_P3.96mm_Vertical; Digikey Part Number 455-B4P-VH-ND
J8: JST_GH_BM04B-GHS; JST_GH_BM04B-GHS-TBT_1x04-1MP_P1.25mm_Vertical; Digikey Part Number 455-1566-2-ND
J10: JST_GH_BM02B-GHS-TBT_1x02-1MP_P1.25mm_Vertical; Digikey Part Number 455-1564-2-ND
J11: BM04B-JST-GH; JST_GH_BM04B-GHS-TBT_1x04-1MP_P1.25mm_Vertical; Digikey Part Number 455-1566-2-ND
J12: Micro_SD_Card_Det2; microSD_HC_Molex_104031-0811; Digikey Part Number WM6357TR-ND
JP1, JP2: SolderJumper_2_Open; SolderJumper-2_P1.3mm_Open_RoundedPad1.0x1.5mm
JP3, JP4, JP5, JP6, JP7, JP8: SolderJumper_3_Open; SolderJumper-3_P1.3mm_Open_RoundedPad1.0x1.5mm_NumberLabels
LED1: LED; LED_0603_1608Metric_Pad1.05x0.95mm_HandSolder; Digikey Part Number 2679-CTL0603FYW1TTR-ND
Q1: 2N7002K; SOT-23; Digikey Part Number 2N7002KTR-ND
R1, R2, R3, R6, R7, R12, R13, R17, R18, R23, R24, R27, R28: 100; R_0603_1608Metric_Pad0.98x0.95mm_HandSolder; Digikey Part Number 311-100GRTR-ND
R4, R8, R15, R19, R25, R29: 10k; R_0603_1608Metric_Pad0.98x0.95mm_HandSolder; Digikey Part Number 13-RC0603FR-1310KLTR-ND
R5, R16: 4.3k; R_0603_1608Metric_Pad0.98x0.95mm_HandSolder; Digikey Part Number P4.30KHTR-ND
R9: 500k; R_0805_2012Metric; Digikey Part Number 738-RNCF0805BTE500KTR-ND
R10: 2.2k; R_0603_1608Metric_Pad0.98x0.95mm_HandSolder; Digikey Part Number 311-2.2KGRTR-ND
R11: 1.5k; R_0603_1608Metric_Pad0.98x0.95mm_HandSolder; Digikey Part Number 408-1766-2-ND
R14, R21, R22: 1k; R_0603_1608Metric_Pad0.98x0.95mm_HandSolder; Digikey Part Number 311-1.0KGRTR-ND
R20, R30: 7.5k; R_0603_1608Metric_Pad0.98x0.95mm_HandSolder; Digikey Part Number 311-7.5KDTR-ND
R26: 13k; R_0603_1608Metric_Pad0.98x0.95mm_HandSolder; Digikey Part Number 541-13.0KHTR-ND
TP1: Conn_01x03; PinHeader_1x03_P2.54mm_Vertical; Digikey Part Number 732-5316-ND
TP2, TP3, TP4, TP5, TP6, TP7: TEST POINT; PinHeader_1x02_P2.54mm_Vertical; Digikey Part Number 732-5315-ND
TP8: PinHeader_1x04_P2.54mm_Vertical; Digikey Part Number 732-5317-ND
TP9: Conn_01x02; PinHeader_1x02_P2.54mm_Vertical; Digikey Part Number 732-5315-ND
U1: UM3232EEAE; SSOP-16_5.3x6.2mm_P0.65mm; Digikey Part Number UM3232EEAE
U2, U3, U5, U7, U8, U9: MCP96L00T-E_MX; QFN65P500X500X100-21N_MCP96L00T-E_MX; Digikey Part Number MCP96L00T-E/MXTR-ND
U4: AQV252G3A; SMDIP-6_W7.62mm; Digikey Part Number 255-6561-ND
U6: TLV1117LV33DCYR; SOT-223-3_TabPin2; Digikey Part Number 296-28778-2-ND
U10: Pico_2_W; RaspberryPi_Pico_Common_THT; Digikey Part Number 2648-SC1633CT-ND
U11: FSM300; FSM300_FOOTPRINT; Digikey Part Number 1888-1001-ND
U12: H3LIS100DLTR; LGA-16_3x3mm_P0.5mm_LayoutBorder3x5y; Digikey Part Number 497-15697-2-ND
U13: LR62XE; Digikey Part Number 1914-LR62XETR-ND

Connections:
+3V3: C1.2, C5.1, C9.1, C12.1, C15.1, C17.1, C19.1, C21.1, C22.1, C23.1, C24.1, J11.3, J12.4 (VDD), JP7.1 (A), JP8.3 (B), R2.1, R4.1, R8.1, R15.1, R19.1, R21.1, R22.1, R25.1, R29.1, U1.16 (VCC), U2.8 (VDD), U3.8 (VDD), U5.8 (VDD), U6.2 (VO), U7.8 (VDD), U8.8 (VDD), U9.8 (VDD), U11.1 (VDD), U12.1 (VDD_IO), U12.8 (CS), U12.14 (VDD), U12.15 (VDD__1), U13.5 (VDD_RADIO)
+5V: C16.1, J2.3, J4.2, J6.2, J8.3, J9.2, JP3.3 (B), JP4.3 (B), TP1.3, U6.3 (VI), U10.39 (VSYS), U13.11 (+5V)
/BOOTN: TP8.3, U11.6 (BOOTN)
/FSM300_RESET: TP8.1, U11.18 (RST)
/H3_INT1: TP9.1, U12.11 (INT1)
/H3_INT2: TP9.2, U12.9 (INT2)
/HINTN: TP8.4, U11.5 (HINTN)
/IRIDIUM_R232: J3.2, U1.8 (R1IN)
/IRIDIUM_T232: J3.1, U1.7 (T1OUT)
/KREM_DETECT: J7.3, J10.1, R14.1
/LORA_ANTSW: TP3.2, U10.26 (GPIO20), U13.1 (ANT-SW)
/LORA_BUSY: TP2.2, U10.29 (GPIO22), U13.3 (BUSY)
/LORA_DIO1: TP2.1, U10.31 (GPIO26_ADC0), U13.4 (DIO1)
/LORA_SPI_CLK: TP4.1, U10.24 (GPIO18), U13.6 (SCK)
/LORA_SPI_CSN: TP5.2, U10.22 (GPIO17), U13.9 (NSS)
/LORA_SPI_MISO: TP5.1, U10.21 (GPIO16), U13.8 (MISO)
/LORA_SPI_MOSI: TP4.2, U10.25 (GPIO19), U13.7 (MOSI)
/PS1: TP8.2, U11.7 (PS1)
/PWMLS: J4.1, J6.1, J9.1, U10.32 (GPIO27_ADC1)
/RX1: J8.1, U10.7 (GPIO5)
/RX_GPS: J1.2, JP2.2 (B), JP6.1 (A)
/RX_GPS_232: JP2.1 (A), U1.13 (R2IN)
/RX_GPS_CONVERT_232: JP6.3 (B), U1.12 (R2OUT)
/R_IRIDIUM: U1.9 (R1OUT), U10.2 (GPIO1)
/SCL: J11.1, R21.2, TP6.1, U2.19 (SCL), U3.19 (SCL), U5.19 (SCL), U7.19 (SCL), U8.19 (SCL), U9.19 (SCL), U10.5 (GPIO3), U11.12 (SCL), U12.4 (SCL/SPC)
/SDA: J11.2, R22.2, TP6.2, U2.20 (SDA), U3.20 (SDA), U5.20 (SDA), U7.20 (SDA), U8.20 (SDA), U9.20 (SDA), U10.4 (GPIO2), U11.11 (SDA), U12.6 (SDA/SDI/SDO)
/SD_SPI_CLK: J12.5 (CLK), U10.19 (GPIO14)
/SD_SPI_CS: J12.2 (DAT3/CD), U10.17 (GPIO13)
/SD_SPI_MISO: J12.7 (DAT0), U10.16 (GPIO12)
/SD_SPI_MOSI: J12.3 (CMD), U10.20 (GPIO15)
/TX1: J8.2, U10.6 (GPIO4)
/TX_GPS: J1.1, JP1.2 (B), JP5.1 (A)
/TX_GPS_232: JP1.1 (A), U1.14 (T2OUT)
/TX_GPS_CONVERT_232: JP5.3 (B), U1.11 (T2IN)
/T_IRIDIUM: U1.10 (T1IN), U10.1 (GPIO0)
/VIN: J2.2, J7.2, JP3.1 (A), JP4.1 (A), TP1.1, U4.4
/VIN_PRE: C10.2, J5.2, R9.2, TP1.2, U4.1, U4.6
/~LORA_RESET: TP3.1, U10.27 (GPIO21), U13.2 (SX-NRESET)
GND: C1.1, C3.1, C5.2, C7.1, C9.2, C10.1, C12.2, C13.1, C15.2, C16.2, C17.2, C19.2, C21.2, C22.2, C23.2, C24.2, H5.1, H6.1, H7.1, H9.1, H11.1, H12.1, J1.4, J2.1, J3.4, J4.3, J5.1, J6.3, J7.1, J7.4, J8.4, J9.3, J10.2, J11.4, J12.6 (VSS), J12.11 (SHIELD), JP7.3 (B), JP8.1 (A), LED1.1 (K), Q1.2 (S), R5.1, R10.1, R16.1, R20.1, R26.1, R30.1, TP7.1, TP7.2, U1.15 (GND), U2.1 (GND), U2.3 (GND__1), U2.5 (GND__2), U2.6 (GND__3), U2.7 (GND__4), U2.9 (GND__5), U2.10 (GND__6), U2.13 (GND__7), U2.17 (GND__8), U2.18 (GND__9), U2.21 (EXP), U2.22 (EXP__1), U2.23 (EXP__2), U2.24 (EXP__3), U2.25 (EXP__4), U2.26 (EXP__5), U2.27 (EXP__6), U2.28 (EXP__7), U2.29 (EXP__8), U2.30 (EXP__9), U3.1 (GND), U3.3 (GND__1), U3.5 (GND__2), U3.6 (GND__3), U3.7 (GND__4), U3.9 (GND__5), U3.10 (GND__6), U3.13 (GND__7), U3.17 (GND__8), U3.18 (GND__9), U3.21 (EXP), U3.22 (EXP__1), U3.23 (EXP__2), U3.24 (EXP__3), U3.25 (EXP__4), U3.26 (EXP__5), U3.27 (EXP__6), U3.28 (EXP__7), U3.29 (EXP__8), U3.30 (EXP__9), U5.1 (GND), U5.3 (GND__1), U5.5 (GND__2), U5.6 (GND__3), U5.7 (GND__4), U5.9 (GND__5), U5.10 (GND__6), U5.13 (GND__7), U5.17 (GND__8), U5.18 (GND__9), U5.21 (EXP), U5.22 (EXP__1), U5.23 (EXP__2), U5.24 (EXP__3), U5.25 (EXP__4), U5.26 (EXP__5), U5.27 (EXP__6), U5.28 (EXP__7), U5.29 (EXP__8), U5.30 (EXP__9), U6.1 (GND), U7.1 (GND), U7.3 (GND__1), U7.5 (GND__2), U7.6 (GND__3), U7.7 (GND__4), U7.9 (GND__5), U7.10 (GND__6), U7.13 (GND__7), U7.17 (GND__8), U7.18 (GND__9), U7.21 (EXP), U7.22 (EXP__1), U7.23 (EXP__2), U7.24 (EXP__3), U7.25 (EXP__4), U7.26 (EXP__5), U7.27 (EXP__6), U7.28 (EXP__7), U7.29 (EXP__8), U7.30 (EXP__9), U8.1 (GND), U8.3 (GND__1), U8.5 (GND__2), U8.6 (GND__3), U8.7 (GND__4), U8.9 (GND__5), U8.10 (GND__6), U8.13 (GND__7), U8.17 (GND__8), U8.18 (GND__9), U8.21 (EXP), U8.22 (EXP__1), U8.23 (EXP__2), U8.24 (EXP__3), U8.25 (EXP__4), U8.26 (EXP__5), U8.27 (EXP__6), U8.28 (EXP__7), U8.29 (EXP__8), U8.30 (EXP__9), U9.1 (GND), U9.3 (GND__1), U9.5 (GND__2), U9.6 (GND__3), U9.7 (GND__4), U9.9 (GND__5), U9.10 (GND__6), U9.13 (GND__7), U9.17 (GND__8), U9.18 (GND__9), U9.21 (EXP), U9.22 (EXP__1), U9.23 (EXP__2), U9.24 (EXP__3), U9.25 (EXP__4), U9.26 (EXP__5), U9.27 (EXP__6), U9.28 (EXP__7), U9.29 (EXP__8), U9.30 (EXP__9), U10.3 (GND), U10.8 (GND), U10.13 (GND), U10.18 (GND), U10.23 (GND), U10.28 (GND), U10.33 (AGND), U10.38 (GND), U11.2 (GND@1), U11.8 (GND@2), U11.9 (PS0_WAKEN), U12.5 (GND), U12.10 (GND__1), U12.12 (GND__2), U12.13 (GND__3), U12.16 (GND__4), U13.10 (GND), U13.12 (GND)
unnamed: H1.1, R1.1
unnamed: H2.1, R3.1
unnamed: H3.1, R6.1
unnamed: H4.1, R7.1
unnamed: H8.1, R12.1
unnamed: H10.1, R13.1
unnamed: H13.1, R17.1
unnamed: H14.1, R18.1
unnamed: H15.1, R23.1
unnamed: H16.1, R24.1
unnamed: H17.1, R27.1
unnamed: H18.1, R28.1
unnamed: J1.3, JP3.2 (C)
unnamed: J3.3, JP4.2 (C)
unnamed: JP5.2 (C), U10.9 (GPIO6)
unnamed: JP6.2 (C), U10.10 (GPIO7)
unnamed: JP7.2 (C), U11.14 (SA0)
unnamed: JP8.2 (C), U12.7 (SDO/SA0)
unnamed: LED1.2 (A), R2.2
unnamed: Q1.3 (D), R11.1
unnamed: C13.2, Q1.1 (G), R9.1, R14.2
unnamed: R11.2, U4.2
unnamed: C2.2, U1.1 (C1+)
unnamed: C2.1, U1.3 (C1-)
unnamed: C6.2, U1.4 (C2+)
unnamed: C6.1, U1.5 (C2-)
unnamed: C3.2, U1.2 (V+)
unnamed: C7.2, U1.6 (V-)
unnamed: R4.2, R5.2, U2.16 (ADDR)
unnamed: C4.1, R1.2, U2.2 (VIN+)
unnamed: C4.2, R3.2, U2.4 (VIN-)
unnamed: R8.2, R10.2, U3.16 (ADDR)
unnamed: C8.1, R6.2, U3.2 (VIN+)
unnamed: C8.2, R7.2, U3.4 (VIN-)
unnamed: R15.2, R16.2, U5.16 (ADDR)
unnamed: C11.1, R12.2, U5.2 (VIN+)
unnamed: C11.2, R13.2, U5.4 (VIN-)
unnamed: R19.2, R20.2, U7.16 (ADDR)
unnamed: C14.1, R17.2, U7.2 (VIN+)
unnamed: C14.2, R18.2, U7.4 (VIN-)
unnamed: R25.2, R26.2, U8.16 (ADDR)
unnamed: C18.1, R23.2, U8.2 (VIN+)
unnamed: C18.2, R24.2, U8.4 (VIN-)
unnamed: R29.2, R30.2, U9.16 (ADDR)
unnamed: C20.1, R27.2, U9.2 (VIN+)
unnamed: C20.2, R28.2, U9.4 (VIN-)

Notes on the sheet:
Indicator LEDs
Test Pads
Short TX_GPS/RX_GPS when using 3.3V levels for the GPS module Short the CONVERT_232 lines when using a GPS with RS232 levels
ADDR=0x67
I2C Header, intended to go to I2C mux for pressure sensors
ADDR=0x63
I2c pull-up resistors
Rs232 level shifted UART for use with Iridium modem. Power rail select jumper for 5v regulator or raw VIN
RS232 Converter
This two pin header serves as a connection point to the spring steel pieces that stick out of the backshell and make contact with the KREM. When the KREM is intact, KREM_DETECT shorted to to ground. When the KREM separates, KREM_DETECT is pulled to VIN_PRE by a weak pull-up resistor
The interrupt and sync signals from the IMUs and H3LIS100 are broken out here for probing. There is no electrical connection from these pins to the main MCU due to pin limitations.
External activation header
ADDR=0x62
FSM300 9-axis IMU
Mounting Holes
Optional connection to external power input
1W LoRa Radio
Testpoints for system voltages VIN is the high voltage pack positive node after being switched by the photoMOS VIN_PRE is the high voltage pack positive node before being switched by the photoMOS 5V is the output node of the 5V regulator. The photoMOS must be enabled to supply this rail
Board to board connections
Depending on jumper settings, this port either provides access to a 3.3VTTL UART or the same UART but shifted to RS232 levels
BNO080 precalibrated module. Solder jumper selects LSB of I2C address (low=0, high=1). ADDR=0x4A or 0x4B
ADDR=0x64
H3LIS100 +/- 100g 3 axis accelerometer
3.3V TTL UART for connection to other subsystems or use as GPIO if no serial port needed.
ADDR=0x61
Headers for Parachute Deployment System
Short SJs when using RS232 levels
Raspberry Pi Pico 2 W RP2350A, 4MB Flash
On this connector, the wires for pin 1 and 2 should go to the power source's voltage output and ground. Pins 3 and 4 should be shorted out by a wire on the connector. This will keep the photoMOS off and prevent back-feeding power into the battery while the connector is present.
3.3V Step Down Voltage Regulator
Interrupt Test Pads
The MOSFET will be low impedance when KREM_DETECT is not shorted to ground. This will let current through the LED in the photoMOS, which will connect the battery. When KREM_DETECT is shorted to ground, the MOSFET will be high impedance, blocking current from flowing through the LED in the photoMOS,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
Solder jumper selects LSB of I2C address (low=0, high=1)
Connection to 3S lithium battery pack.
TC to Digital Converters
Battery Pack Power Switch
Battery and power connections
Connection to external 5v regulator
MicroSD Card
ADDR=0x60

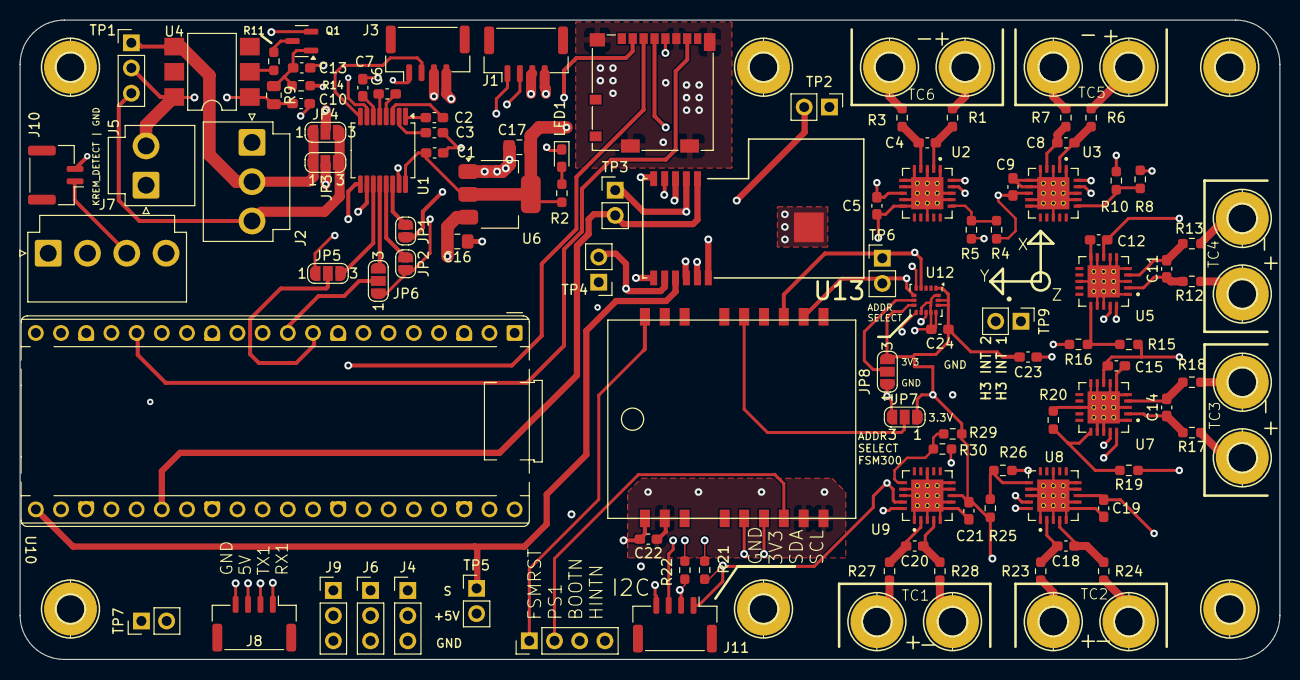
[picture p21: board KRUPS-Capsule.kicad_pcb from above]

Board: 6 copper layers, 127.0 x 64.4 mm, 116 parts (0 on the bottom side), 85 nets.

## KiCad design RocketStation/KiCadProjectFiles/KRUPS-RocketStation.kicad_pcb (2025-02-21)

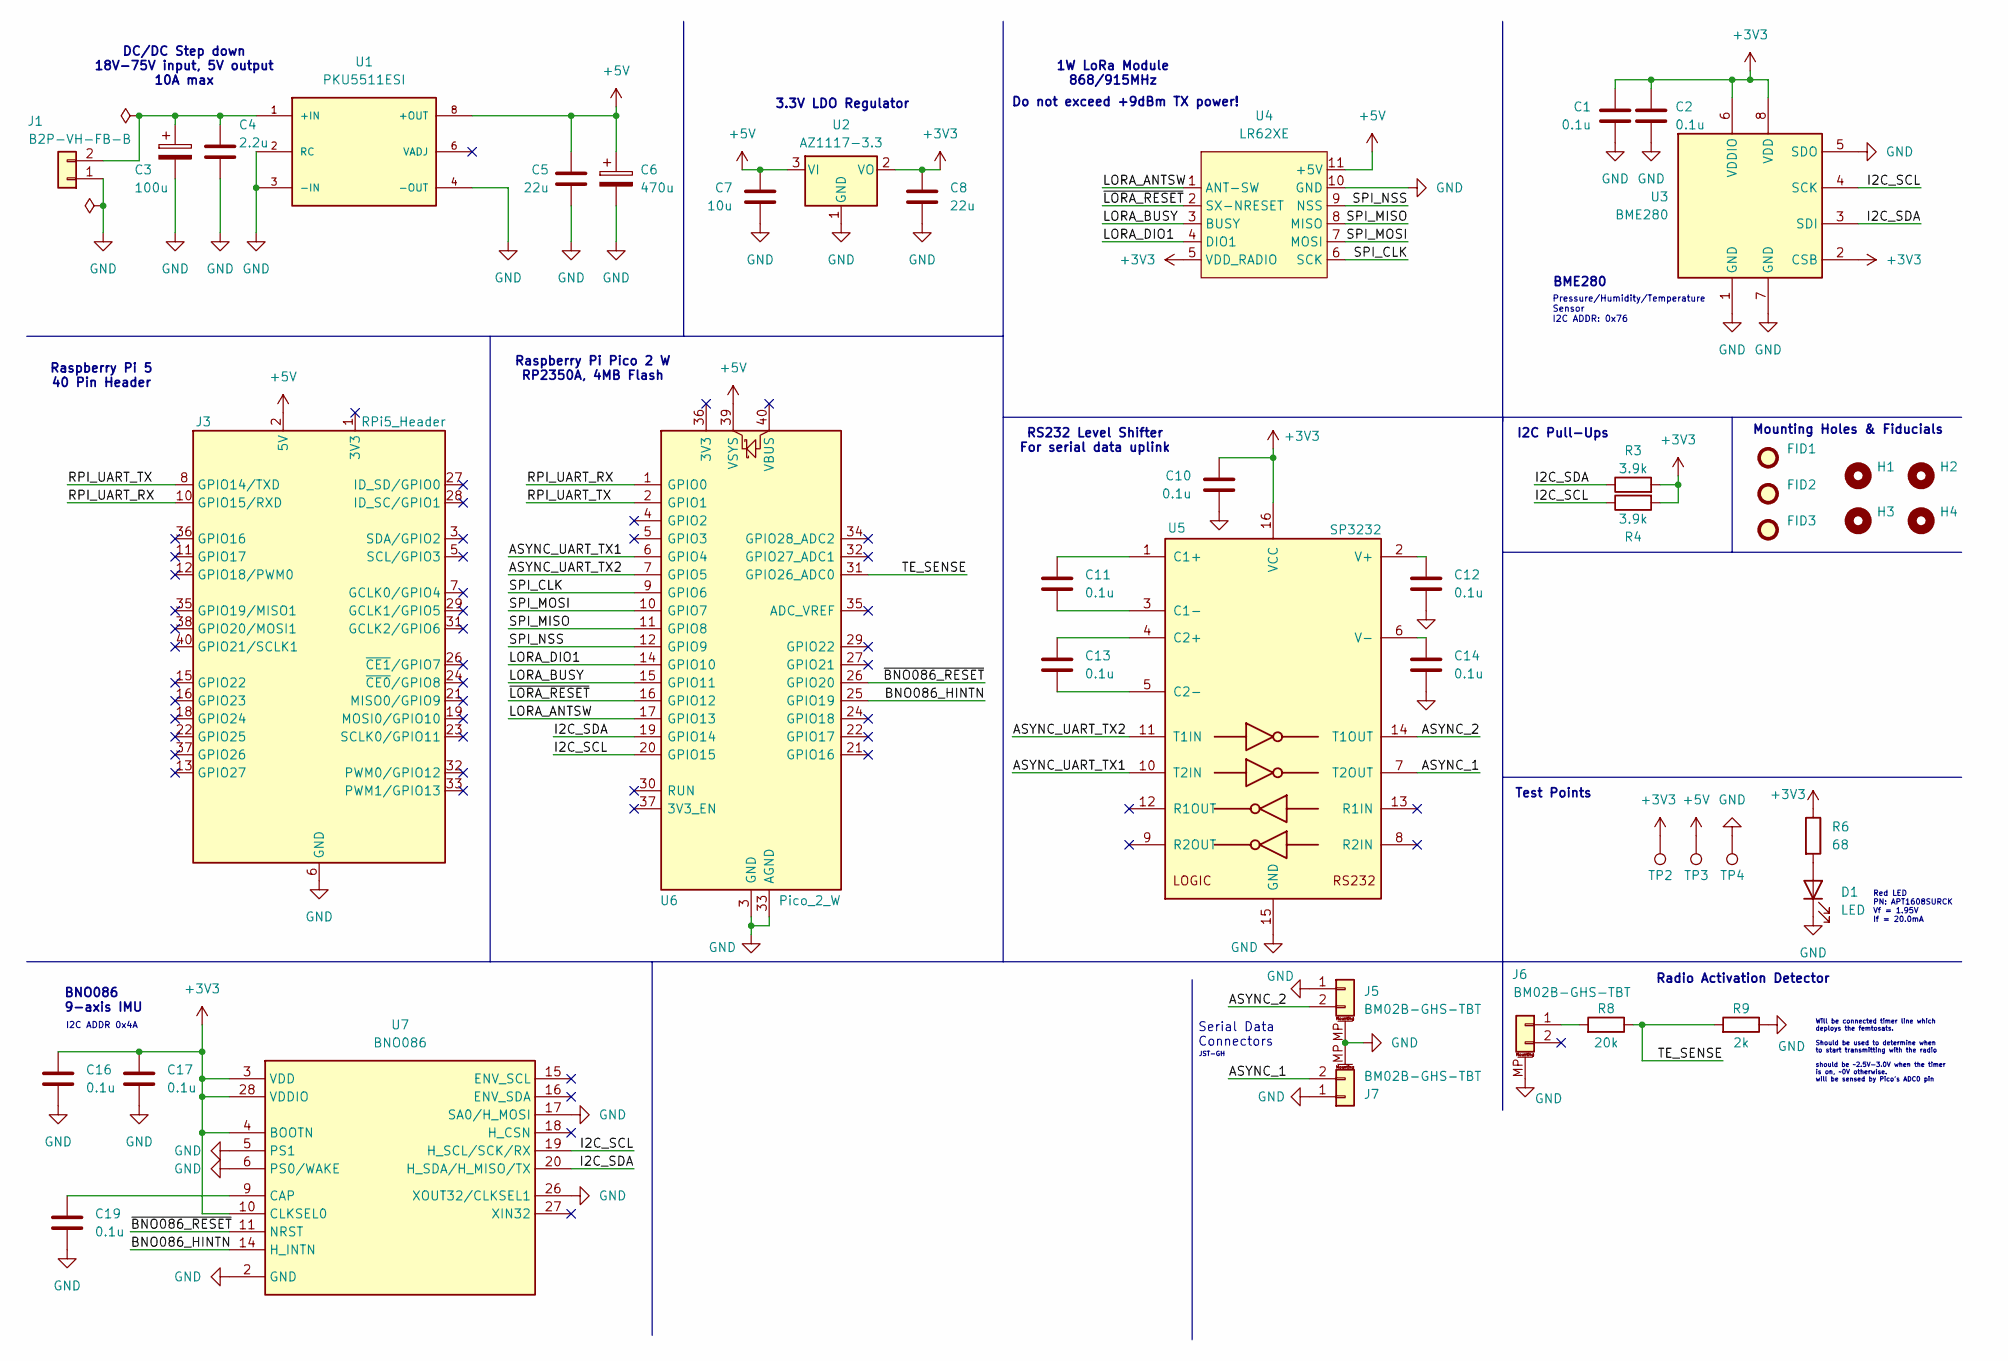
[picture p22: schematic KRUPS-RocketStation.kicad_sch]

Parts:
C1, C2, C10, C11, C12, C13, C14, C16, C17, C19: 0.1u; C_0603_1608Metric_Pad1.08x0.95mm_HandSolder; Digikey Part Number CC0603KRX7R7BB104
C3: 100u; A768MS_Anti_Vibration; Digikey Part Number A768MS107M1JLAV027
C4: 2.2u; C_1206_3216Metric_Pad1.33x1.80mm_HandSolder; Digikey Part Number 12061C225KAT2A
C5, C8: 22u; C_0805_2012Metric_Pad1.18x1.45mm_HandSolder; Digikey Part Number CL21A226MPQNNNE
C6: 470u; A768MS_Anti_Vibration; Digikey Part Number A768MS477M1ELAV017
C7: 10u; C_0805_2012Metric_Pad1.18x1.45mm_HandSolder; Digikey Part Number CL21A106KOQNNNG
D1: LED; D_0603_1608Metric_Pad1.05x0.95mm_HandSolder; Digikey Part Number APT1608SURCK
FID1, FID2, FID3: Fiducial; Fiducial_0.75mm_Mask1.5mm
H1: MountingHole; MountingHole_2.7mm_M2.5
H2, H3, H4: MountingHole; MountingHole_2.7mm_M2.5_Pad
J1: B2P-VH-FB-B; JST_VH_B2P-VH-FB-B_1x02_P3.96mm_Vertical; Digikey Part Number B2P-VH-FB-B
J3: RPi5_Header; PinSocket_2x20_P2.54mm_Vertical; Digikey Part Number PRT-16764
J5, J6, J7: BM02B-GHS-TBT; JST_GH_BM02B-GHS-TBT_1x02-1MP_P1.25mm_Vertical; Digikey Part Number BM02B-GHS-TBT
R3, R4: 3.9k; R_0603_1608Metric_Pad0.98x0.95mm_HandSolder; Digikey Part Number ERJ-3EKF3901V
R6: 68; R_0603_1608Metric_Pad0.98x0.95mm_HandSolder; Digikey Part Number RC0603JR-0768RL
R8: 20k; R_0603_1608Metric_Pad0.98x0.95mm_HandSolder; Digikey Part Number ERJ-3EKF2002V
R9: 2k; R_0603_1608Metric_Pad0.98x0.95mm_HandSolder; Digikey Part Number ERJ-3EKF2001V
TP2, TP3, TP4: TestPoint; PinHeader_1x01_P2.54mm_Vertical
U1: PKU5511ESI; CONV_PKU5511ESI; Digikey Part Number PKU5511ESI
U2: AZ1117-3.3; SOT-89-3_Handsoldering; Digikey Part Number AZ1117CR2-3.3TRG1
U3: BME280; Bosch_LGA-8_2.5x2.5mm_P0.65mm_ClockwisePinNumbering; Digikey Part Number BME280
U4: LR62XE
U5: SP3232; TSSOP-16_4.4x5mm_P0.65mm; Digikey Part Number SP3232EUEY-L/TR
U6: Pico_2_W; RaspberryPi_Pico_Common_THT
U7: BNO086; LGA-28_5.2x3.8mm_P0.5mm; Manufacturer_Part_Number BNO086; Mouser Part Number 526-BNO086

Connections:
+3V3: C1.1, C2.1, C8.1, C10.1, C16.1, C17.1, R3.2, R4.2, R6.1, TP2.1, U2.2 (VO), U3.2 (CSB), U3.6 (VDDIO), U3.8 (VDD), U4.5 (VDD_RADIO), U5.16 (VCC), U7.3 (VDD), U7.4 (BOOTN), U7.10 (CLKSEL0), U7.28 (VDDIO)
+5V: C5.1, C6.1, C7.1, J3.2 (5V), J3.4 (5V), TP3.1, U1.8 (+OUT), U2.3 (VI), U4.11 (+5V), U6.39 (VSYS)
/ASYNC_1: J7.2, U5.7 (T2OUT)
/ASYNC_2: J5.2, U5.14 (T1OUT)
/ASYNC_UART_TX1: U5.10 (T2IN), U6.6 (GPIO4)
/ASYNC_UART_TX2: U5.11 (T1IN), U6.7 (GPIO5)
/BNO086_HINTN: U6.25 (GPIO19), U7.14 (H_INTN)
/I2C_SCL: R4.1, U3.4 (SCK), U6.20 (GPIO15), U7.19 (H_SCL/SCK/RX)
/I2C_SDA: R3.1, U3.3 (SDI), U6.19 (GPIO14), U7.20 (H_SDA/H_MISO/TX)
/LORA_ANTSW: U4.1 (ANT-SW), U6.17 (GPIO13)
/LORA_BUSY: U4.3 (BUSY), U6.15 (GPIO11)
/LORA_DIO1: U4.4 (DIO1), U6.14 (GPIO10)
/RPI_UART_RX: J3.10 (GPIO15/RXD), U6.1 (GPIO0)
/RPI_UART_TX: J3.8 (GPIO14/TXD), U6.2 (GPIO1)
/SPI_CLK: U4.6 (SCK), U6.9 (GPIO6)
/SPI_MISO: U4.8 (MISO), U6.11 (GPIO8)
/SPI_MOSI: U4.7 (MOSI), U6.10 (GPIO7)
/SPI_NSS: U4.9 (NSS), U6.12 (GPIO9)
/TE_SENSE: R8.1, R9.2, U6.31 (GPIO26_ADC0)
/~BNO086_RESET: U6.26 (GPIO20), U7.11 (NRST)
/~LORA_RESET: U4.2 (SX-NRESET), U6.16 (GPIO12)
GND: C1.2, C2.2, C3.2, C4.2, C5.2, C6.2, C7.2, C8.2, C10.2, C12.2, C14.2, C16.2, C17.2, C19.2, D1.1 (K), J1.1, J3.6 (GND), J3.9 (GND), J3.14 (GND), J3.20 (GND), J3.25 (GND), J3.30 (GND), J3.34 (GND), J3.39 (GND), J5.1, J5.MP (MountPin), J6.MP (MountPin), J7.1, J7.MP (MountPin), R9.1, TP4.1, U1.2 (RC), U1.3 (-IN), U1.4 (-OUT), U2.1 (GND), U3.1 (GND), U3.5 (SDO), U3.7 (GND), U4.10 (GND), U4.12 (GND), U5.15 (GND), U6.3 (GND), U6.8 (GND), U6.13 (GND), U6.18 (GND), U6.23 (GND), U6.28 (GND), U6.33 (AGND), U6.38 (GND), U7.2 (GND), U7.5 (PS1), U7.6 (PS0/WAKE), U7.17 (SA0/H_MOSI), U7.25 (GND), U7.26 (XOUT32/CLKSEL1)
unnamed: D1.2 (A), R6.2
unnamed: C3.1, C4.1, J1.2, U1.1 (+IN)
unnamed: J6.1, R8.2
unnamed: C11.1, U5.1 (C1+)
unnamed: C11.2, U5.3 (C1-)
unnamed: C13.1, U5.4 (C2+)
unnamed: C13.2, U5.5 (C2-)
unnamed: C12.1, U5.2 (V+)
unnamed: C14.1, U5.6 (V-)
unnamed: C19.1, U7.9 (CAP)

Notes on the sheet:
Pressure/Humidity/Temperature Sensor I2C ADDR: 0x76
1W LoRa Module 868/915MHz
RS232 Level Shifter For serial data uplink
3.3V LDO Regulator
I2C Pull-Ups
Red LED PN: APT1608SURCK Vf = 1.95V If = 20.0mA
Test Points
Radio Activation Detector
Serial Data Connectors
Do not exceed +9dBm TX power!
Mounting Holes & Fiducials
I2C ADDR 0x4A
Raspberry Pi 5 40 Pin Header
BME280
DC/DC Step down 18V-75V input, 5V output 10A max
BNO086 9-axis IMU
Will be connected timer line which deploys the femtosats. Should be used to determine when to start transmitting with the radio should be ~2.5V-3.0V when the timer is on, ~0V otherwise. will be sensed by Pico's ADC0 pin
Raspberry Pi Pico 2 W RP2350A, 4MB Flash
JST-GH

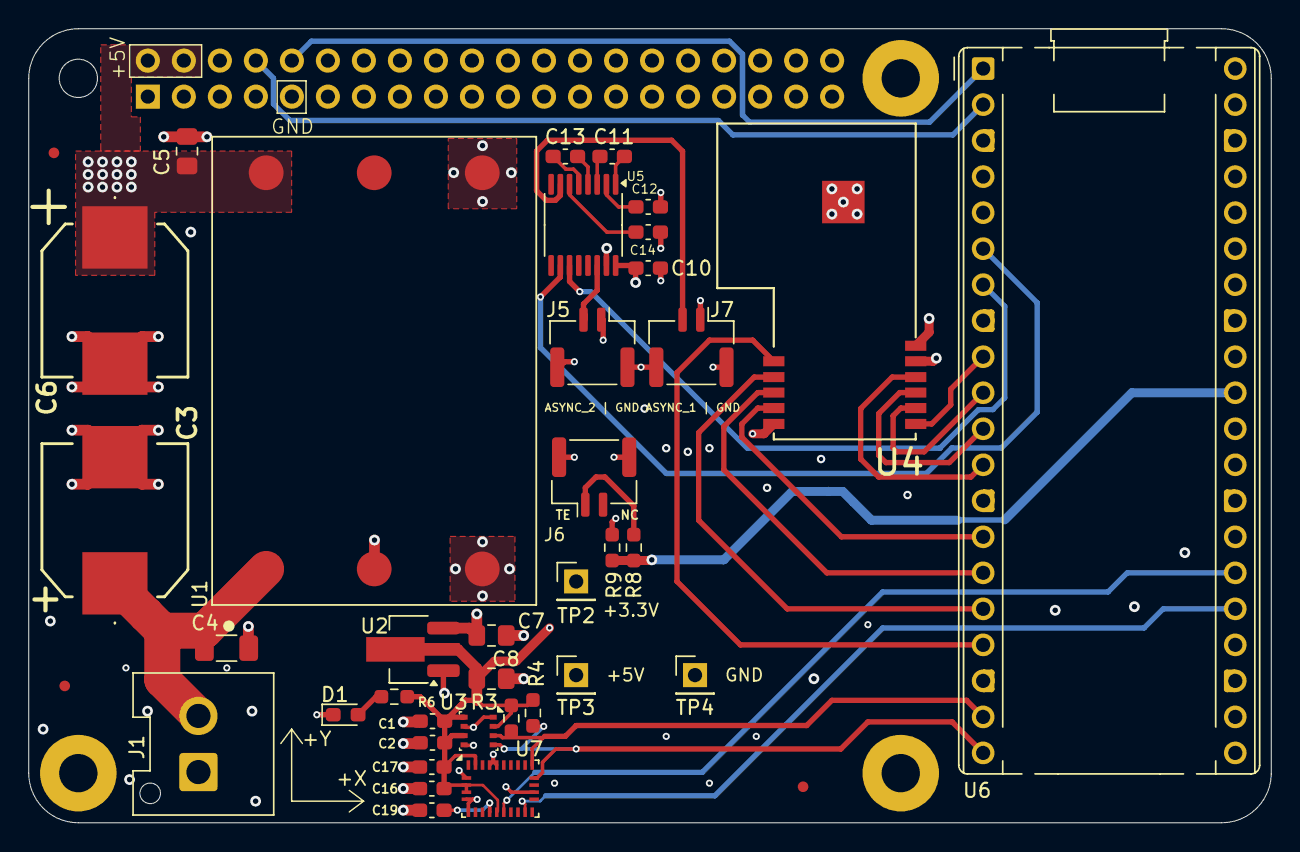
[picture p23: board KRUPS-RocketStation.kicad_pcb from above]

Board: 4 copper layers, 87.6 x 56.0 mm, 44 parts (1 on the bottom side), 32 nets.

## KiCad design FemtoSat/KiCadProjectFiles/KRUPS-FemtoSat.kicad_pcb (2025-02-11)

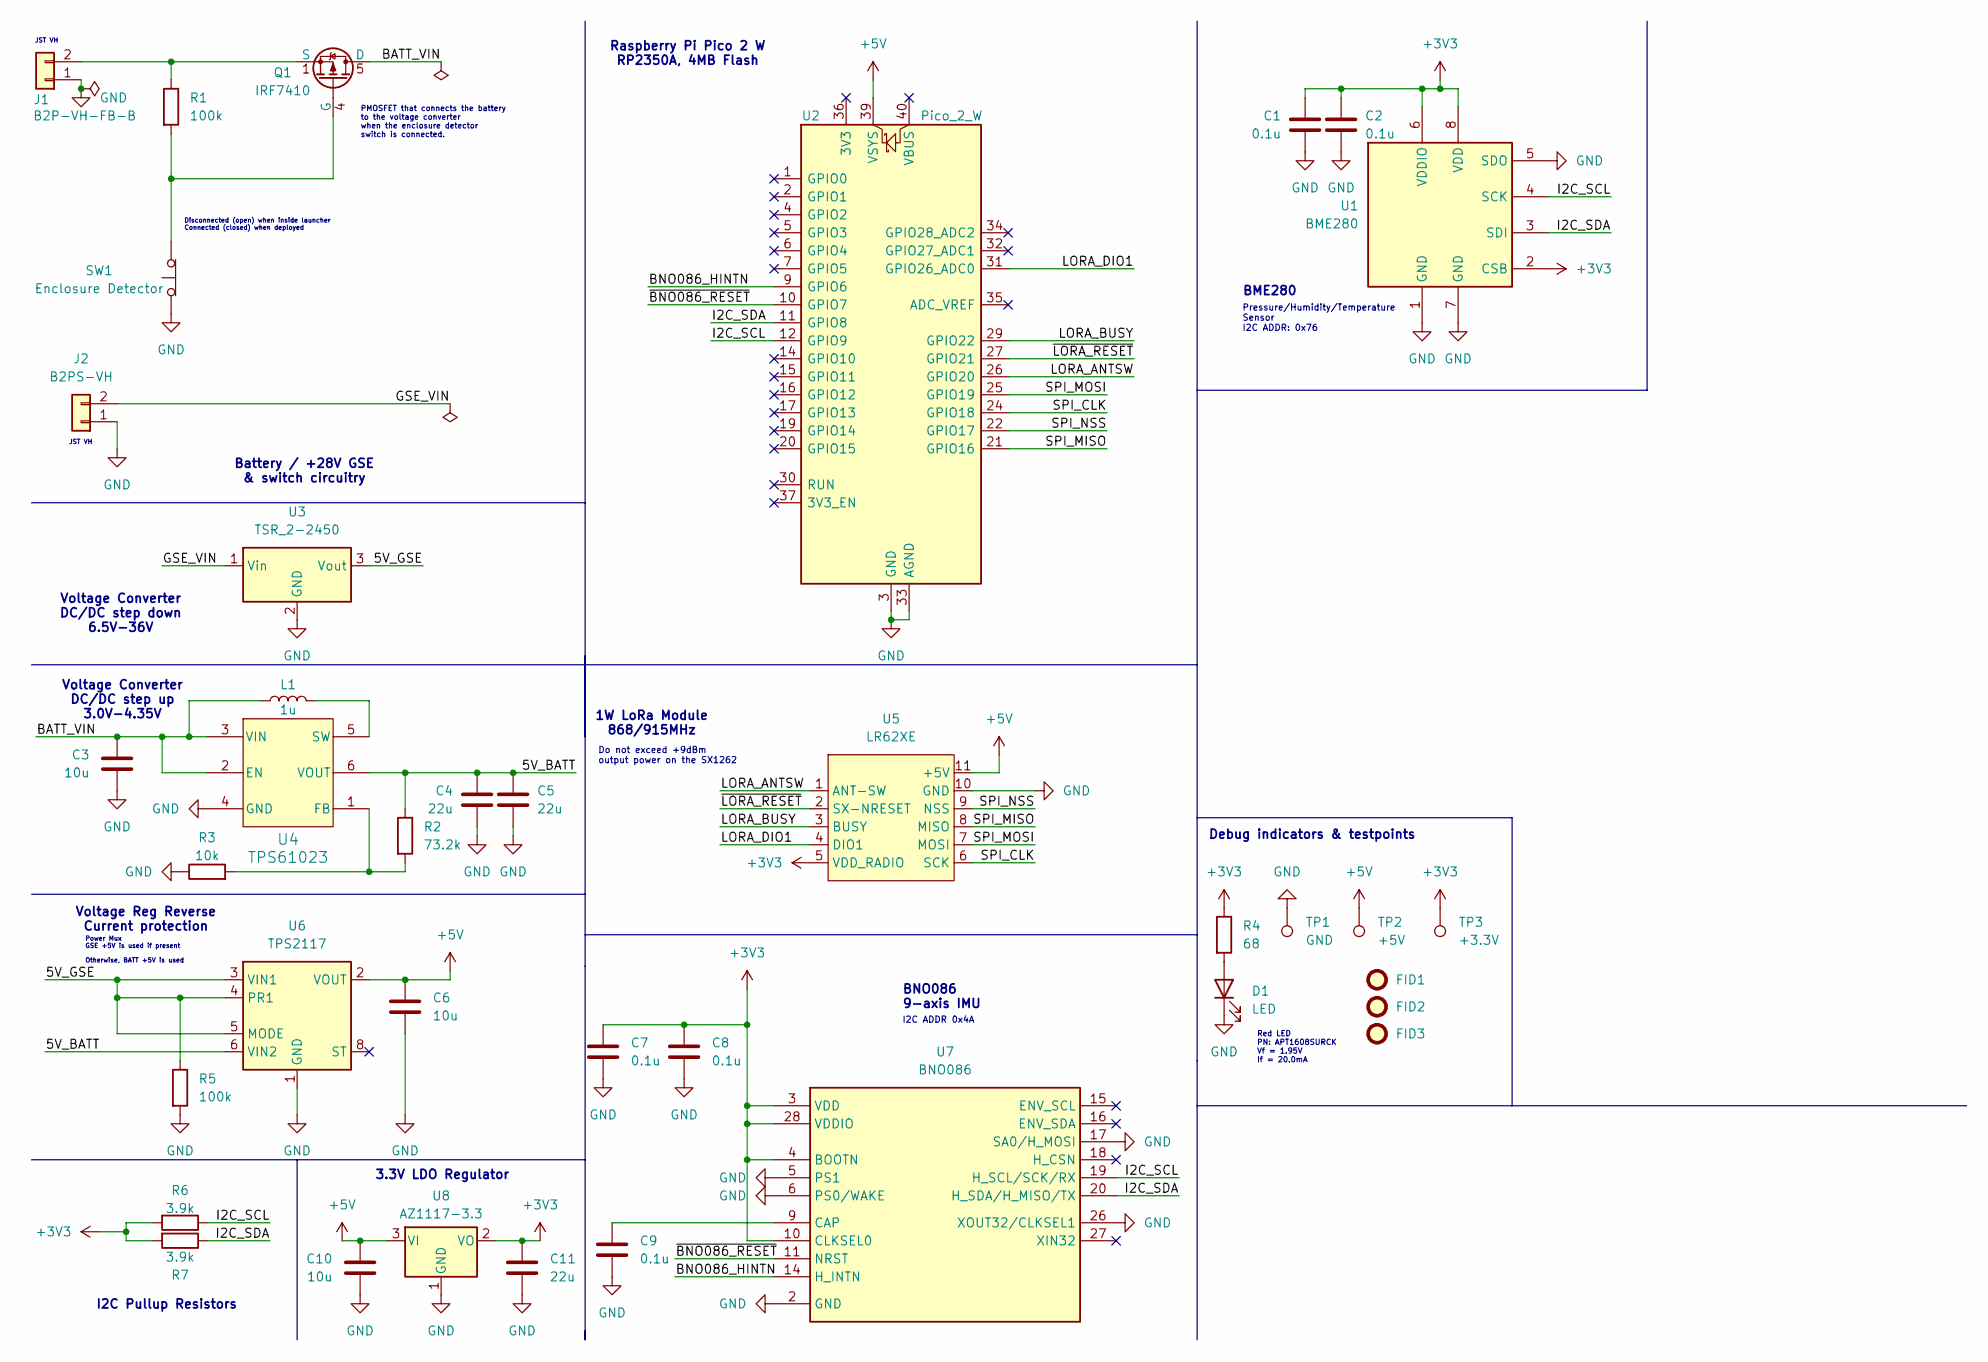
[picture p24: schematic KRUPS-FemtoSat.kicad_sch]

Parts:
C1, C2, C7, C8, C9: 0.1u; C_0603_1608Metric_Pad1.08x0.95mm_HandSolder; Digikey Part Number CC0603KRX7R7BB104
C3, C6, C10: 10u; C_0805_2012Metric_Pad1.18x1.45mm_HandSolder; Digikey Part Number CL21A106KOQNNNG
C4, C5, C11: 22u; C_0805_2012Metric_Pad1.18x1.45mm_HandSolder; Digikey Part Number CL21A226MPQNNNE
D1: LED; D_0603_1608Metric_Pad1.05x0.95mm_HandSolder; Digikey Part Number APT1608SURCK
FID1, FID2, FID3: Fiducial; Fiducial_0.5mm_Mask1mm
J1: B2P-VH-FB-B; JST_VH_B2P-VH-FB-B_1x02_P3.96mm_Vertical; Digikey Part Number B2P-VH-FB-B
J2: B2PS-VH; JST_VH_S2P-VH_1x02_P3.96mm_Horizontal; Digikey Part Number B2PS-VH
L1: 1u; L_Coilcraft_XxL4030; Digikey Part Number XEL4030-102MEC
Q1: IRF7410; SOIC-8_3.9x4.9mm_P1.27mm; Digikey Part Number IRF7410TRPBF
R1, R5: 100k; R_0603_1608Metric_Pad0.98x0.95mm_HandSolder; Digikey Part Number RMCF0603FT100K
R2: 73.2k; R_0603_1608Metric_Pad0.98x0.95mm_HandSolder; Digikey Part Number RC0603FR-0773K2L
R3: 10k; R_0603_1608Metric_Pad0.98x0.95mm_HandSolder; Digikey Part Number RC0603FR-0710KL
R4: 68; R_0603_1608Metric_Pad0.98x0.95mm_HandSolder; Digikey Part Number RC0603JR-0768RL
R6, R7: 3.9k; R_0603_1608Metric_Pad0.98x0.95mm_HandSolder; Digikey Part Number ERJ-3EKF3901V
SW1: Enclosure Detector; LC1258OANP; Digikey Part Number LC1258OANP
TP1: GND; TestPoint_Pad_2.0x2.0mm
TP2: +5V; TestPoint_Pad_2.0x2.0mm
TP3: +3.3V; TestPoint_Pad_2.0x2.0mm
U1: BME280; Bosch_LGA-8_2.5x2.5mm_P0.65mm_ClockwisePinNumbering; Digikey Part Number BME280
U2: Pico_2_W; RaspberryPi_Pico2_W_SMD; Digikey Part Number 2648-SC1633CT-ND
U3: TSR_2-2450; CONV_TSR_2-2450; Digikey Part Number TSR 2-2450
U4: TPS61023; SOT-563; Digikey Part Number TPS61023DRLR
U5: LR62XE; Digikey Part Number LR62XE
U6: TPS2117; SOT-583-8; Digikey Part Number TPS2117DRLR
U7: BNO086; LGA-28_5.2x3.8mm_P0.5mm; Manufacturer_Part_Number BNO086; Mouser Part Number 526-BNO086
U8: AZ1117-3.3; SOT-89-3_Handsoldering; Digikey Part Number AZ1117CR2-3.3TRG1

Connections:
+3V3: C1.1, C2.1, C7.1, C8.1, C11.1, R4.1, R6.2, R7.2, TP3.1, U1.2 (CSB), U1.6 (VDDIO), U1.8 (VDD), U5.5 (VDD_RADIO), U7.3 (VDD), U7.4 (BOOTN), U7.10 (CLKSEL0), U7.28 (VDDIO), U8.2 (VO)
+5V: C6.1, C10.1, TP2.1, U2.39 (VSYS), U5.11 (+5V), U6.2 (VOUT), U6.7 (VOUT), U8.3 (VI)
/5V_BATT: C4.1, C5.1, R2.1, U4.6 (VOUT), U6.6 (VIN2)
/5V_GSE: R5.1, U3.3 (Vout), U6.3 (VIN1), U6.4 (PR1), U6.5 (MODE)
/BATT_VIN: C3.1, L1.1, Q1.5 (D), Q1.6, Q1.7, Q1.8, U4.2 (EN), U4.3 (VIN)
/BNO086_HINTN: U2.9 (GPIO6), U7.14 (H_INTN)
/GSE_VIN: J2.2, U3.1 (Vin)
/I2C_SCL: R6.1, U1.4 (SCK), U2.12 (GPIO9), U7.19 (H_SCL/SCK/RX)
/I2C_SDA: R7.1, U1.3 (SDI), U2.11 (GPIO8), U7.20 (H_SDA/H_MISO/TX)
/LORA_ANTSW: U2.26 (GPIO20), U5.1 (ANT-SW)
/LORA_BUSY: U2.29 (GPIO22), U5.3 (BUSY)
/LORA_DIO1: U2.31 (GPIO26_ADC0), U5.4 (DIO1)
/SPI_CLK: U2.24 (GPIO18), U5.6 (SCK)
/SPI_MISO: U2.21 (GPIO16), U5.8 (MISO)
/SPI_MOSI: U2.25 (GPIO19), U5.7 (MOSI)
/SPI_NSS: U2.22 (GPIO17), U5.9 (NSS)
/~BNO086_RESET: U2.10 (GPIO7), U7.11 (NRST)
/~LORA_RESET: U2.27 (GPIO21), U5.2 (SX-NRESET)
GND: C1.2, C2.2, C3.2, C4.2, C5.2, C6.2, C7.2, C8.2, C9.2, C10.2, C11.2, D1.1 (K), J1.1, J2.1, R3.1, R5.2, SW1.1 (A), TP1.1, U1.1 (GND), U1.5 (SDO), U1.7 (GND), U2.3 (GND), U2.8 (GND), U2.13 (GND), U2.18 (GND), U2.23 (GND), U2.28 (GND), U2.33 (AGND), U2.38 (GND), U3.2 (GND), U4.4 (GND), U5.10 (GND), U5.12 (GND), U6.1 (GND), U7.2 (GND), U7.5 (PS1), U7.6 (PS0/WAKE), U7.17 (SA0/H_MOSI), U7.25 (GND), U7.26 (XOUT32/CLKSEL1), U8.1 (GND)
unnamed: D1.2 (A), R4.2
unnamed: J1.2, Q1.1 (S), Q1.2, Q1.3, R1.1
unnamed: Q1.4 (G), R1.2, SW1.2 (B)
unnamed: R2.2, R3.2, U4.1 (FB)
unnamed: L1.2, U4.5 (SW)
unnamed: C9.1, U7.9 (CAP)

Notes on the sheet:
Power Mux GSE +5V is used if present Otherwise, BATT +5V is used
I2C ADDR 0x4A
JST VH
Red LED PN: APT1608SURCK Vf = 1.95V If = 20.0mA
Pressure/Humidity/Temperature Sensor I2C ADDR: 0x76
3.3V LDO Regulator
I2C Pullup Resistors
Voltage Converter DC/DC step down 6.5V-36V
Disconnected (open) when inside launcher Connected (closed) when deployed
Battery / +28V GSE & switch circuitry
PMOSFET that connects the battery to the voltage converter when the enclosure detector switch is connected.
Voltage Reg Reverse Current protection
BNO086 9-axis IMU
BME280
Do not exceed +9dBm output power on the SX1262
Raspberry Pi Pico 2 W RP2350A, 4MB Flash
Debug indicators & testpoints
1W LoRa Module 868/915MHz
Voltage Converter DC/DC step up 3.0V-4.35V

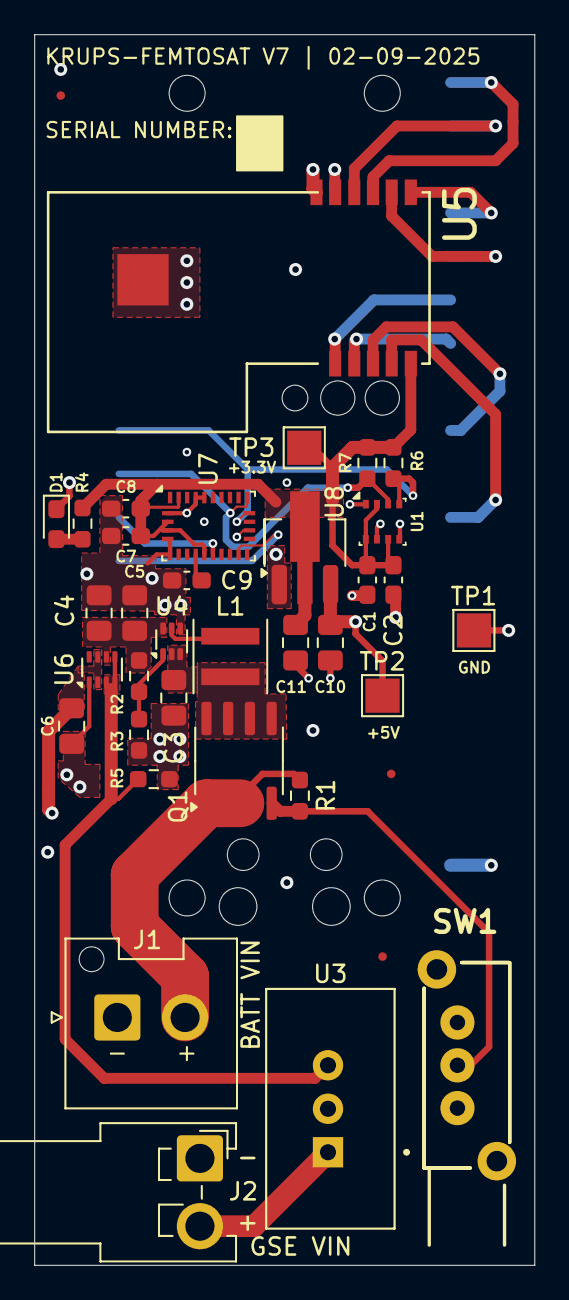
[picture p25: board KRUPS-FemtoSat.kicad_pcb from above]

Board: 4 copper layers, 29.2 x 71.9 mm, 38 parts (1 on the bottom side), 25 nets.

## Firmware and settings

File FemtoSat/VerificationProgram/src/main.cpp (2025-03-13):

#include <stdio.h>
#include "pico/stdlib.h"

// IMU
#include "bno08x.h"
#include "utils.h"  // BNO08X driver related

// BME280
extern "C" {    // extern because drivers are .c files
#include "bme280_driver.h"
}

// LoRa
#include "hardware/spi.h"
#include "RadioLib.h"
#include "hal/RPiPico/PicoHal.h"

// WiFi modem
#ifdef CYW43_WL_GPIO_LED_PIN
#include "pico/cyw43_arch.h"
#endif

// I2C defines
#define I2C_PORT i2c0           // i2c port. shared between BME280 & BNO08X
#define I2C_SDA 8        // gpio pin for i2c SDA
#define I2C_SCL 9        // gpio pin for i2c SCL
#define I2C_SPEED 400000 // i2c bus speed, 400KHz

// SPI defines. only used for radio
// TO-DO: update this to match femtosat pinout
// right now it's set to whatever my breadboard is wired up to
#define SPI_PORT spi0
#define PIN_MISO 16
#define PIN_MOSI 19
#define PIN_SCK 18
#define PIN_CS 17
#define PIN_DIO1 26
#define PIN_RST 21
#define PIN_BUSY 22

// LoRa defines
// see https://unsigned.io/understanding-lora-parameters/

// TO-DO: update parameters for LR62XE
// these are set for the LAMBDA62 lora breakouts we have and 
// not the LR62XE that we're actually using.
#define LORA_FREQ               915.0
#define LORA_BANDWIDTH          500.0
#define LORA_SPREADINGFACTOR    9
#define LORA_CODINGRATE         7
#define LORA_SYNCWORD           RADIOLIB_SX126X_SYNC_WORD_PRIVATE // 0x12
#define LORA_TX_POWER           -9      // in dBm. DO NOT EXCEED 9 dBm! 
                                        // set to lowest option (-9dBm) to prevent overcurrent on USB power
#define LORA_PREAMBLE_LENGTH    8
#define LORA_TXCO_VOLTAGE       0
#define LORA_USE_LDO            false


// BME280
#define BME280_ADDR 0x76        // i2c address of the BME280


int main()
{
    stdio_init_all();
    cyw43_arch_init();

    // turn on light to show you things are happening
    cyw43_arch_gpio_put(CYW43_WL_GPIO_LED_PIN, 1);
    sleep_ms(500);

    // I2C Initialization
    i2c_init(I2C_PORT, I2C_SPEED);
    gpio_set_function(I2C_SDA, GPIO_FUNC_I2C);
    gpio_set_function(I2C_SCL, GPIO_FUNC_I2C);
    gpio_pull_up(I2C_SDA);
    gpio_pull_up(I2C_SCL);

    // volatile variables showing initialization states. inspect these with debugger!
    volatile int loraInitState;         // 0 means successful init
    volatile int8_t bme280InitState;    // 0 means successful init
    volatile bool BNO086InitState;      // TRUE means it initialized successfully

    // initialize sensors

    // lora
    PicoHal myHal(SPI_PORT, PIN_MISO, PIN_MOSI, PIN_SCK);
    SX1262 radio = SX1262(new Module( & myHal, PIN_CS, PIN_DIO1, PIN_RST, PIN_BUSY));
    loraInitState= radio.begin(
        LORA_FREQ, 
        LORA_BANDWIDTH, 
        LORA_SPREADINGFACTOR, 
        LORA_CODINGRATE, 
        LORA_SYNCWORD, 
        LORA_TX_POWER, 
        LORA_PREAMBLE_LENGTH, 
        LORA_TXCO_VOLTAGE, 
        LORA_USE_LDO
    );
    sleep_ms(100);

    // bme280
    struct bme280_inst bme280;
    bme280InitState = bme280_init(
        I2C_PORT,
        BME280_ADDR,
        &bme280,
        BME280_FORCED_MODE,
        BME280_FILTER_OFF,
        BME280_T_OVERSAMPLE_1,
        BME280_H_OVERSAMPLE_1,
        BME280_P_OVERSAMPLE_1
    );
    sleep_ms(100);

    // bno086
    BNO08x IMU;
    BNO086InitState = IMU.begin(CONFIG::BNO08X_ADDR, I2C_PORT);

    // shut off LED if everything initializes successfully
    // BREAKPOINT HERE
    if ((loraInitState == RADIOLIB_ERR_NONE) && (bme280InitState == BME280_OK) && (BNO086InitState == true)) {
        cyw43_arch_gpio_put(CYW43_WL_GPIO_LED_PIN, 0);
    }

    // otherwise, make LED blink for eternity
    else {
        while(true) {
            cyw43_arch_gpio_put(CYW43_WL_GPIO_LED_PIN, 1);
            sleep_ms(1000);
            cyw43_arch_gpio_put(CYW43_WL_GPIO_LED_PIN, 0);
            sleep_ms(1000);
        }
    }
    while(1){};
}

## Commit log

2024-10-29 V1 Commit
    Initial V1 Design
    [54-00170.step, E22-900M33S.STEP, ESP32-S3-WROOM-1U-N16R8.step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]
2024-10-31 V1.1 Update
    - Replaced the ESP32-S3-WROOM-1U module with an ESP32-S3-WROOM-2 module (octal SPI flash, integrated PCB antenna)
    - Changed the pins assigned to LORA_TXEN/RXEN to avoid possible issues with 1.8V logic levels on IO47 & IO48
    - Updated relevant documentation
    [ESP32-S3-WROOM-1U-N16R8.step, ESP32-S3-WROOM-2-N32R8V.step, FemtoSat_BOM.csv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]
2024-10-31 changed version marker on back silkscreen to v1.1
    [KRUPS-FemtoSat.kicad_pcb]
2024-11-11 V2 Update. Added mounting holes, moved around some components, and added some silkscreen markers
    [KRUPS-FemtoSat.kicad_pcb, KRUPS-FemtoSat.kicad_sch]
2024-11-11 V3. Connected the SPI NSS of the LoRa modem to an IO pin rather than ground
    [KRUPS-FemtoSat.kicad_pcb, KRUPS-FemtoSat.kicad_sch]
2024-11-17 Reorganized repository, added initial files for the GHOST RocketStation
    - Changed the repository name from KRUPS-FemtoSat to RockSatX-GHOST-Hardware
    - Reorganized the repository, each individual PCB now gets its own folder
    - Added V1 files for the KRUPS-RocketStation
    [54-00170.step, A768MS.step, B2P-VH-FB-B.STEP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]
2024-11-17 Small fixes for RocketStation v1
    Modified RocketStation readme, fixed unconnected 3.3V test point, slightly changed async nets on schematic
    [KRUPS-RocketStation.kicad_pcb, KRUPS-RocketStation.kicad_sch]
2024-11-21 Updated femtosat/rocketstation BOMs
    [FemtoSat_BOM.csv, RocketStation_BOM.csv]
2024-12-05 Added optional support for the LR62XE 1W radio
    - Created a breakout/adapter board for the LR62XE 1W LoRa radio
    - Modified the FemtoSat and RocketStation so that they'll be compatible with the adapter board
    [FemtoSat_BOM.csv, KRUPS-FemtoSat.kicad_pcb, KRUPS-FemtoSat.kicad_sch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]
2024-12-05 added adapter pictures, changed adapter silkscreen
    [LR62XEAdapter.kicad_pcb]
2024-12-28 Design Review Updates
    Large number of design changes to both the FemtoSat (V5) and RocketStation (V3)
    On both boards:
    - Swapped the ESP32-S3-WROOM-2 modules to WROOM-1 modules due to supply issues
    - Swapped power connectors to JST VH, data connectors to JST GH
    - Added "Space Systems Lab, University of Kentucky, Lexington KY, USA, Earth" to the silkscreens
    - Added test pads for IO pins, I2C bus, power
    - Added LEDs connected to IO pins
    - Changed power indication LEDs to a brighter LED
    - Reformatted BOMs, they can now be generated by KiCad rather than being made by hand
    - Updated documentation, 3D models
    For Femtosat
    - Removed 1 enclosure switch & MOSFET
    - Moved a screw hole
    and a bunch of o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
    [54-00170.step, B2P-VH-FB-B.STEP, FemtoSat_BOM.csv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]
2024-12-28 Added fiducials to femtosat (v6) and rocketstation (v4)
    [KRUPS-FemtoSat.kicad_pcb, KRUPS-FemtoSat.kicad_sch, KRUPS-RocketStation.kicad_pcb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]
2025-01-11 Corrected entries for C3 & C18 (100uF) on RocketStation BOM
    [RocketStation_BOM.csv]
2025-01-22 Corrected part numbers for C3 and C18 in BOM
    [KRUPS-RocketStation.kicad_sch, RocketStation_BOM.csv]
2025-02-11 Changed to Raspi Pico, 1W radio
    - Swapped the ESP32 S3 WROOM to a Raspberry Pi Pico 2 W on both the FemtoSat and RocketStation
    - Swapped to 1W LoRa module in place of the 2W EBYTE one
    - bunch of layout, documentation, miscellaneous changes
    [E22-900M33S.STEP, ESP32-S3-WROOM-2-N32R8V.step, FemtoSat_BOM.csv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]
2025-02-21 Removed LR62XE adapter, corrected readme, fixed silkscreen on LR62XE footprint
    [KRUPS-RocketStation.kicad_pcb, LR62XEAdapter.kicad_pcb, LR62XEAdapter.kicad_sch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]
2025-03-04 Uploaded files for main capsule PCB on the behalf of Cannon Shields
    [KRUPS-Capsule.kicad_pcb, KRUPS-Capsule.kicad_sch]
2025-04-20 updated capsule schematic with improvised thermocouple changes. created schematic pdf
    [KRUPS-Capsule.kicad_sch]
2025-06-24 Adding board render
